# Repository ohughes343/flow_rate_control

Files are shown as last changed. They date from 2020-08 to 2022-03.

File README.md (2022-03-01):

# How To
You will need:
* Lulzbot TAZ 6 - This is the printer I based my design on, but the project could be modified for other printers
* Raspberry Pi - I wrote the code for a raspberry pi computer but with a few tweaks it can run on any computer. Just need a serial connection to the printer and a camera.
* Raspberry Pi HQ Camera
* 16mm lens - To zoom in on the filament
* Backlight - Important for accurate optical measurement. I strapped a flashlight on my printer but there is probably a more elegant solution.
* Red filament - I tuned the software to look for red pixels, but feel free to modify it for other colors

First, print my modified extruder latch and replace the original part with it.<br>

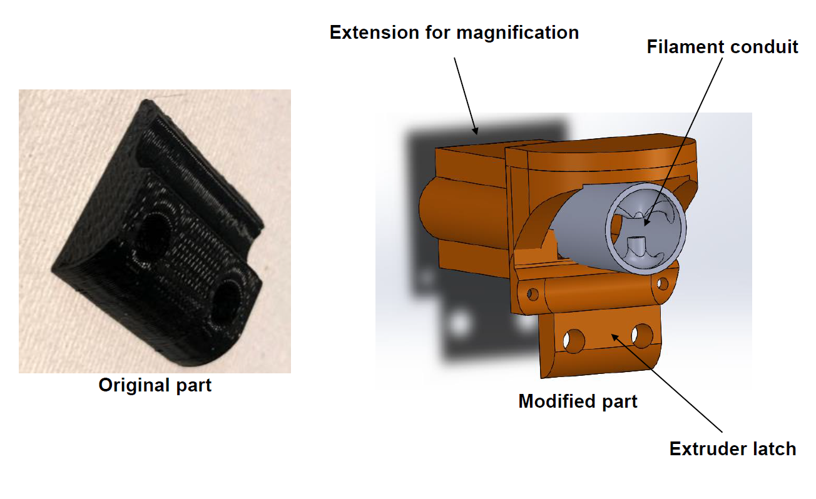
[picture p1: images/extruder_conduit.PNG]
Extruder Conduit


Next, print the extension for the camera lens. This is used to create a "macro" effect and zoom in on the filament. <br>
Be careful not to damage the camera sensor!<br>
Remove the camera lens and unscrew the black piece that holds the lens.<br>
Replace this with the printed extender, and then screw the lens back into that.<br>
You may want to test the camera to get a good zoom - the filament should fill up most of the frame.<br>

Next, download my modded version of pronterface onto your Raspberry Pi:<br>
```git clone https://github.com/ohughes343/flow_rate_control.git```

-Add your gcode file to the folder<br>
-Edit the measure.py file to include your gcode file: (filename="my_file.gcode")<br>
-Connect your Pi to the printer<br>
-Run the script! Print should start automatically<br>

# What is this?

The aim of this project was to produce high-quality prints *regardless of the quality of the filament.* 
Commercially available filament has tight tolerances (Prusa3D claims +/-0.02mm), but experimental filament is often much worse. Inconsistent diameter or consistently off diameter filament results in poor prints with inaccurate dimensions. To remedy this, I measured the filament diameter during printing and adjusted the flow rate accordingly.

This project should be able to print with filament that varies by as much as 0.2mm from its baseline. Outside those dimensions, the printer will have trouble grabbing the filament and may not extrude at all.

**How it works:** A camera attached to the printhead measures the diameter of the filament ten times per second. If the diameter varies too much, a command is sent to the printer to adjust its flow rate. The command is sent after a short delay as it takes some time for that section of filament to reach the nozzle. 
The code is run on a raspberry pi computer and uses pronterface http://www.pronterface.com/index.html

**Materials:**
* Lulzbot TAZ 6 - This is the printer I based my design on, but the project could be modified for other printers
* Raspberry Pi - I wrote the code for a raspberry pi computer but with a few tweaks it can run on any computer. Just need a serial connection to the printer and a camera.
* Raspberry Pi HQ Camera
* 16mm lens - To zoom in on the filament
* Backlight - Important for accurate optical measurement. I strapped a flashlight on my printer but there is probably a more elegant solution.

**Variable Diameter Filament**\
Print quality is related to fill factor, which requires careful control of extrusion rate. When printing, a normal printer assumes constant diameter filament. If diameter is inconsistent, extrudate diameter is also inconsistent.

![Deformed Filament](https://github.com/ohughes343/flow_rate_control/blob/master/images/deformed.JPG)

Tolerances are good for commercially produced filament, as low as ±0.02mm.
For experimental filament, however, the tolerances are typically more like ±0.2mm. This can result in low quality parts that are significantly weaker.

The goal of this project was to print high quality parts using lab-generated filament with ±0.2mm tolerances.

**Objective and Approach**\
Objective: Develop a low-cost, universal hardware and software modification that allows desktop printers to compensate for filament diameter variations

**Producing Variable Diameter Filament**\
I hung a 50cm length of filament and heated it with a hair dryer to produce necked down sections. I was careful to make sure the diameter stayed above 1.55mm, as the printer would not extrudate anything smaller. 

![Hairdryer](https://github.com/ohughes343/flow_rate_control/blob/master/images/hairdryer.png)

**Optical Imaging Setup**\
I purchased a Raspberry Pi 3 computer, an accompanying HQ camera, and a 16mm lens. I also downloaded an [extruder part](https://download.lulzbot.com/TAZ/6.02/production_parts/printed_parts/extruder_latch/) from Lulzbot and modified it to hold the camera and filament in place.

![Extruder Conduit](https://github.com/ohughes343/flow_rate_control/blob/master/images/extruder_conduit.PNG)

![Final setup on printhead](https://github.com/ohughes343/flow_rate_control/blob/master/images/final_setup.PNG)

**Optical Imaging Software**\
Images were captured and analyzed 10 times per second. Since the filament was moving at 1mm/s relative to the camera, 1mm of filament has 10 data points. I implemented a moving average to reduce noise - every data point is an average of itself and the previous 9 points.

![Before and after smoothing](https://github.com/ohughes343/flow_rate_control/blob/master/images/smoothing_graphs.png)

**Adaptive Algorithm**\
![Deformed Filament](https://github.com/ohughes343/flow_rate_control/blob/master/images/equations.png)

![Deformed Filament](https://github.com/ohughes343/flow_rate_control/blob/master/images/equation_graph.png)

**Pixel Size Calibration**\
I took images of filament and a microscope calibration slide at the same distance from the camera to calibrate my software. A 1.79mm diameter chunk of filament took up 508px, which is roughly 0.003mm/px. This is about the best resolution I could get while sampling 10x per second at 640x480. I was able to get 0.001mm/px resolution at lower sampling rates.

![Alt text](https://github.com/ohughes343/flow_rate_control/blob/master/images/filament_hd.JPG)

**Results: Optical Diameter Measurement**\
Measuring *the same* chunk of filament 3 times resulted in the plot on the left, demonstrating that my system is highly precise and repeatable. Some of the smoothing may be due to my software averaging, but it is clearly responding to real physical changes.
The plot on the right demonstrates the same idea with filament that was stretched out to produce very narrow sections.

In both cases, a digital micrometer confirmed the accuracy of the camera. 
![Variable Filament](https://github.com/ohughes343/flow_rate_control/blob/master/images/variable_diameter.png)

**Results: Adaptive Control**\
I implemented a delay in the system to account for the time it takes for the filament to travel from the camera to the nozzle. 
And this is where I got stuck. I first tried to use a time delay, but this wouldn't work for different speeds or if the motor ever retracted filament. A fixed step delay, which I tried next, is also complicated by retraction. So as of right now, the project *works*, but only if the motor never reverses.
![Variable Filament](https://github.com/ohughes343/flow_rate_control/blob/master/images/delay.png)

**My system vs a Keyence Laser**\
One chunk of **lab-produced** filament was measured 3 times with a Keyence digital micrometer. I measured the same chunk 3 times with my optical system to compare the results.
![Experimental](https://github.com/ohughes343/flow_rate_control/blob/master/images/experimental_vs_laser.png)

I made the same comparison with commercial filament.
![As-received](https://github.com/ohughes343/flow_rate_control/blob/master/images/as_received_vs_laser.png)

**Demonstration Part**\
I printed a thin airfoil part to demonstrate my adaptive control.
![Demo part](https://github.com/ohughes343/flow_rate_control/blob/master/images/demo_part.png) 

**Future Work**
* Universal Mount for other 3D printers
* Use with filament colors other than red

![FFF printer](https://github.com/ohughes343/flow_rate_control/blob/master/images/fff.png)

![Lulzbot TAZ 6](https://github.com/ohughes343/flow_rate_control/blob/master/images/taz.png)

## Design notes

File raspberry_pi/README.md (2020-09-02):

# flow_rate_control
If I published a paper it would be called something like *"Autonomous in-situ flow rate control of fused deposition modeling printers"*

Basically, the aim of this project is to produce high-quality prints regardless of the quality of the filament. 
Commercially available filament has tight tolerances (Prusa3D claims +/-0.02mm), but experimental filament is often much worse. Inconsistent diameter or consistently off diameter filament results in poor prints with inaccurate dimensions. There are even designs online to test for over/under extrusion: https://www.thingiverse.com/thing:1622868

This project should be able to print with filament that varies by as much as 0.2mm from its baseline. Outside those dimensions, the printer will have trouble grabbing the filament and may not extrude at all.

**How it works:** A camera attached to the printhead measures the diameter of the filament ten times per second. If the diameter varies too much, a command is sent to the printer to adjust its flow rate accordingly. The command is sent after a short delay, as it takes some time for that section of filament to reach the nozzle. 
The code is run on a raspberry pi computer and uses pronterface http://www.pronterface.com/index.html

**Materials:**
* Lulzbot TAZ 6 - This is just the printer I based my design on but the project could be modified for other printers
* Raspberry Pi - I wrote the code for a raspberry pi computer but with a few tweaks it can run on any computer. Just need a serial connection to the printer and a camera.
* Raspberry Pi HQ Camera
* 16mm lens - To zoom in on the filament
* Backlight - Important for accurate optical measurement. I strapped a flashlight on my printer but there is probably a more elegant solution.

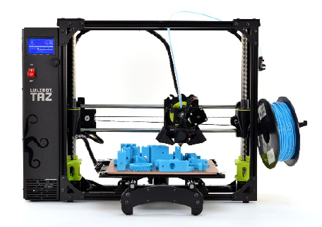
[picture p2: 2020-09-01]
images/taz.png

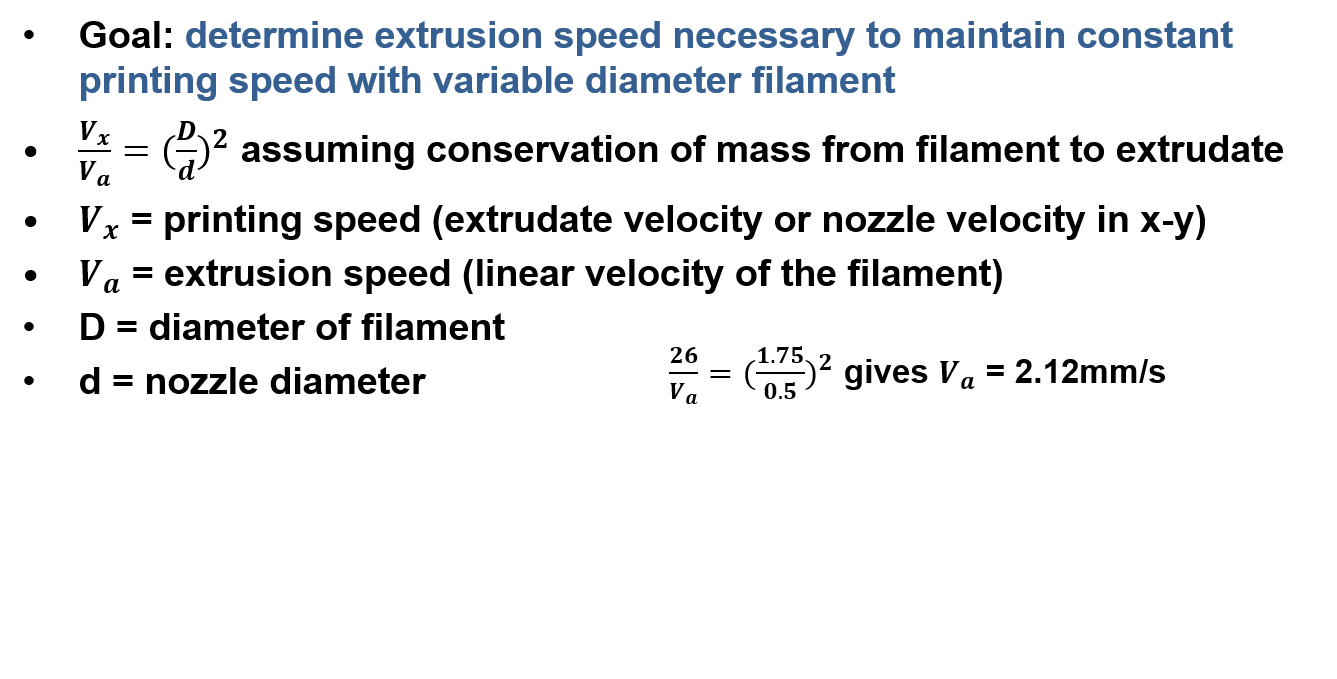
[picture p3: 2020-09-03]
images/equations.png

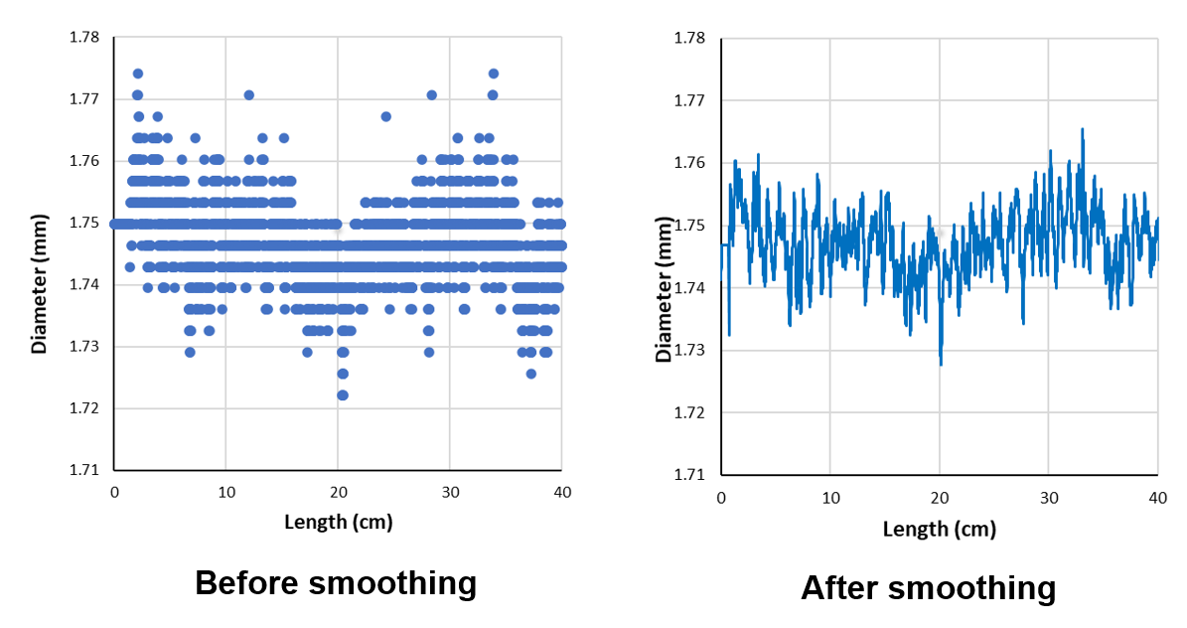
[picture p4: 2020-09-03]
images/smoothing_graphs.png

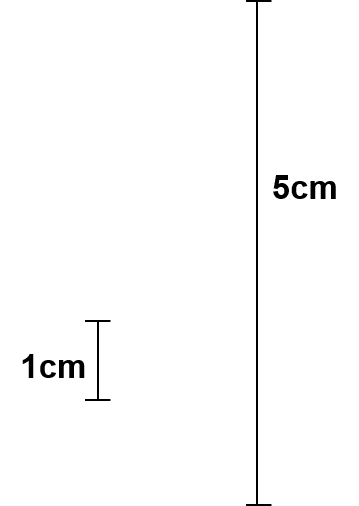
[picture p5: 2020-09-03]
images/filament_51.png

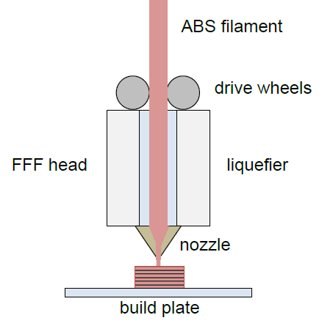
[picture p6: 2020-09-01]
images/fff.png

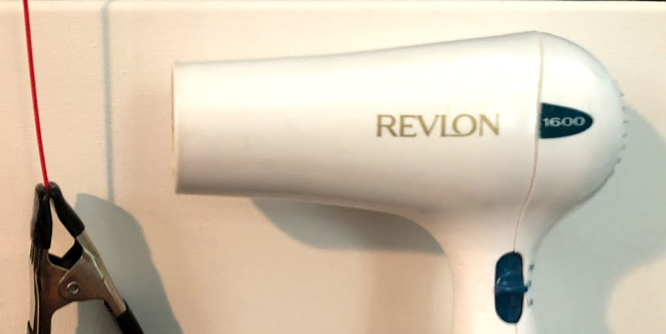
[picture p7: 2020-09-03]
images/hairdryer.png

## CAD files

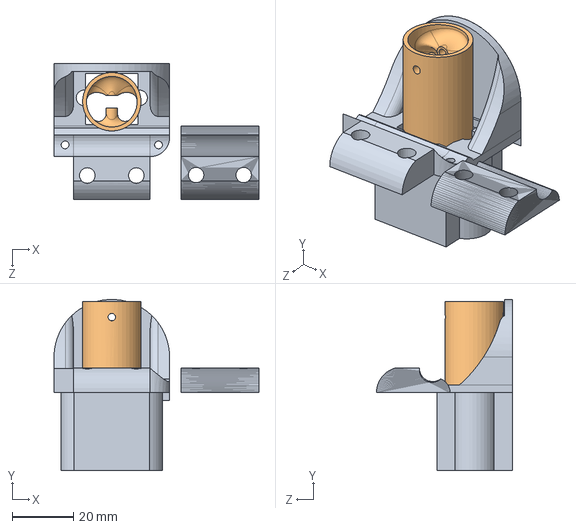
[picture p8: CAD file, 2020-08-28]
CAD files/camera_sleeve.SLDASM
66.8 x 55.8 x 44.4 mm
extruder_latch_largecamera
filament_lens_cap

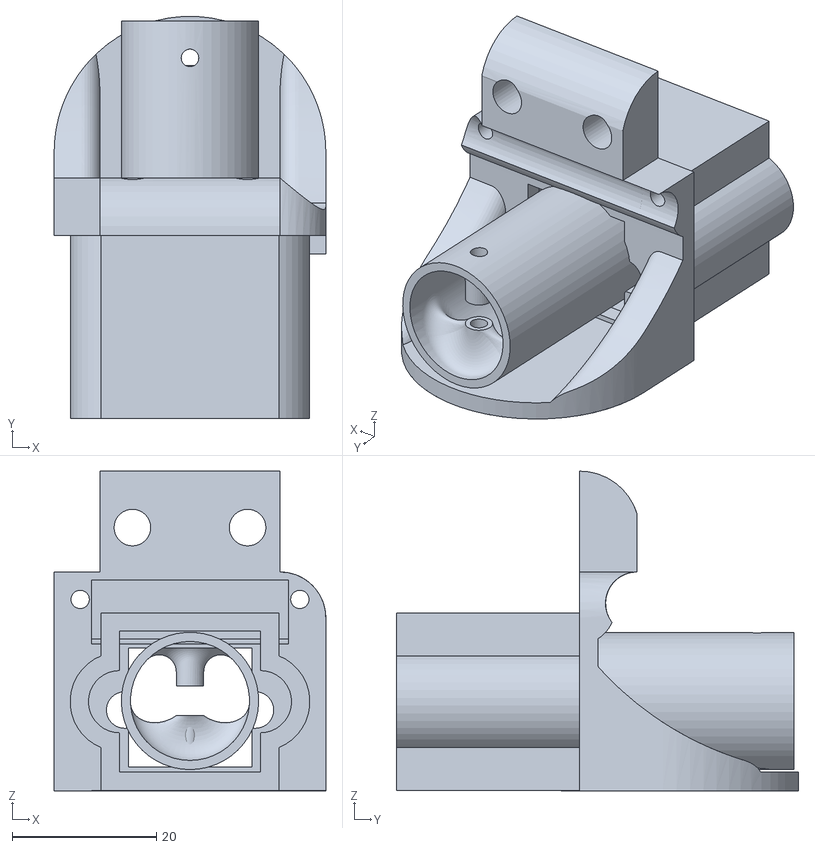
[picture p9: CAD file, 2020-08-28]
CAD files/camera_assembly_full.STL
37.7 x 55.8 x 44.4

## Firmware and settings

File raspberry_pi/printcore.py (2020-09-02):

#!/usr/bin/env python3

# This file is part of the Printrun suite.
#
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
import time
import getopt
import sys
import getopt

from printrun.printcore import printcore
from printrun.utils import setup_logging
from printrun import gcoder

if __name__ == '__main__':
    setup_logging(sys.stderr)
    baud = 250000
    loud = False
    statusreport = False

    from printrun.printcore import __version__ as printcore_version

    usage = "Usage:\n"+\
            "  printcore [OPTIONS] PORT FILE\n\n"+\
            "Options:\n"+\
            "  -b, --baud=BAUD_RATE"+\
                        "\t\tSet baud rate value. Default value is 115200\n"+\
            "  -s, --statusreport\t\tPrint progress as percentage\n"+\
            "  -v, --verbose\t\t\tPrint additional progress information\n"+\
            "  -V, --version\t\t\tPrint program's version number and exit\n"+\
            "  -h, --help\t\t\tPrint this help message and exit\n"

    try:
        opts, args = getopt.getopt(sys.argv[1:], "b:svVh",
                        ["baud=", "statusreport", "verbose", "version", "help"])
    except getopt.GetoptError as err:
        print(str(err))
        print(usage)
        sys.exit(2)
    for o, a in opts:
        if o in ('-h', '--help'):
            print(usage)
            sys.exit(0)
        elif o in ('-V','--version'):
            print("printrun "+printcore_version)
            sys.exit(0)
        elif o in ('-b','--baud'):
            try:
                baud = int(a)
            except ValueError:
                print("ValueError:")
                print("\tInvalid BAUD_RATE value '%s'" % a)
                print("\tBAUD_RATE must be an integer\n")
                # FIXME: This should output a more apropiate error message when
                #        not a good baud rate is passed as an argument
                #        i.e: when baud <= 1000 or > 225000
                print(usage)
                sys.exit(2)
        elif o in ('-v', '--verbose'):
            loud = True
        elif o in ('-s', '--statusreport'):
            statusreport = True

    if len(args) <= 1:
        print("Error: Port or gcode file were not specified.\n")
        print(usage)
        sys.exit(2)
    elif len(args) > 1:
        port = args[-2]
        filename = args[-1]
        print("Printing: %s on %s with baudrate %d" % (filename, port, baud))

    p = printcore(port, baud)
    p.loud = loud
    time.sleep(2)
    gcode = [i.strip() for i in open(filename)]
    gcode = gcoder.LightGCode(gcode)
    p.startprint(gcode)

    try:
        if statusreport:
            p.loud = False
            sys.stdout.write("Progress: 00.0%\r")
            sys.stdout.flush()
        while p.printing:
            time.sleep(1)
            if statusreport:
                progress = 100 * float(p.queueindex) / len(p.mainqueue)
                sys.stdout.write("Progress: %02.1f%%\r" % progress)
                sys.stdout.flush()
        p.disconnect()
        sys.exit(0)
    except:
        p.disconnect()

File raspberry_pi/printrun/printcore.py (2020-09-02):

# This file is part of the Printrun suite.
#
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
__version__ = "2.0.0rc6"

import sys
if sys.version_info.major < 3:
    print("You need to run this on Python 3")
    sys.exit(-1)

from serial import Serial, SerialException, PARITY_ODD, PARITY_NONE
from select import error as SelectError
import threading
from queue import Queue, Empty as QueueEmpty
import time
import platform
import os
import logging
import traceback
import errno
import socket
import re
import selectors
from functools import wraps, reduce
from collections import deque
from printrun import gcoder
from .utils import set_utf8_locale, install_locale, decode_utf8
try:
    set_utf8_locale()
except:
    pass
install_locale('pronterface')
from printrun.plugins import PRINTCORE_HANDLER

def locked(f):
    @wraps(f)
    def inner(*args, **kw):
        with inner.lock:
            return f(*args, **kw)
    inner.lock = threading.Lock()
    return inner

def control_ttyhup(port, disable_hup):
    """Controls the HUPCL"""
    if platform.system() == "Linux":
        if disable_hup:
            os.system("stty -F %s -hup" % port)
        else:
            os.system("stty -F %s hup" % port)

def enable_hup(port):
    control_ttyhup(port, False)

def disable_hup(port):
    control_ttyhup(port, True)

PR_EOF = None  #printrun's marker for EOF
PR_AGAIN = b'' #printrun's marker for timeout/no data
SYS_EOF = b''  #python's marker for EOF
SYS_AGAIN = None #python's marker for timeout/no data

class printcore():
    def __init__(self, port = None, baud = None, dtr=None):
        """Initializes a printcore instance. Pass the port and baud rate to
           connect immediately"""
        self.baud = None
        self.dtr = None
        self.port = None
        self.analyzer = gcoder.GCode()
        # Serial instance connected to the printer, should be None when
        # disconnected
        self.printer = None
        # clear to send, enabled after responses
        # FIXME: should probably be changed to a sliding window approach
        self.clear = 0
        # The printer has responded to the initial command and is active
        self.online = False
        # is a print currently running, true if printing, false if paused
        self.printing = False
        self.mainqueue = None
        self.priqueue = Queue(0)
        self.queueindex = 0
        self.lineno = 0
        self.resendfrom = -1
        self.paused = False
        self.sentlines = {}
        self.log = deque(maxlen = 10000)
        self.sent = []
        self.writefailures = 0
        self.tempcb = None  # impl (wholeline)
        self.recvcb = None  # impl (wholeline)
        self.sendcb = None  # impl (wholeline)
        self.preprintsendcb = None  # impl (wholeline)
        self.printsendcb = None  # impl (wholeline)
        self.layerchangecb = None  # impl (wholeline)
        self.errorcb = None  # impl (wholeline)
        self.startcb = None  # impl ()
        self.endcb = None  # impl ()
        self.onlinecb = None  # impl ()
        self.loud = False  # emit sent and received lines to terminal
        self.tcp_streaming_mode = False
        self.greetings = ['start', 'Grbl ']
        self.wait = 0  # default wait period for send(), send_now()
        self.read_thread = None
        self.stop_read_thread = False
        self.send_thread = None
        self.stop_send_thread = False
        self.print_thread = None
        self.readline_buf = []
        self.selector = None
        self.event_handler = PRINTCORE_HANDLER
        # Not all platforms need to do this parity workaround, and some drivers
        # don't support it.  Limit it to platforms that actually require it
        # here to avoid doing redundant work elsewhere and potentially breaking
        # things.
        self.needs_parity_workaround = platform.system() == "linux" and os.path.exists("/etc/debian")
        for handler in self.event_handler:
            try: handler.on_init()
            except: logging.error(traceback.format_exc())
        if port is not None and baud is not None:
            self.connect(port, baud)
        self.xy_feedrate = None
        self.z_feedrate = None

    def addEventHandler(self, handler):
        '''
        Adds an event handler.
        
        @param handler: The handler to be added.
        '''
        self.event_handler.append(handler)

    def logError(self, error):
        for handler in self.event_handler:
            try: handler.on_error(error)
            except: logging.error(traceback.format_exc())
        if self.errorcb:
            try: self.errorcb(error)
            except: logging.error(traceback.format_exc())
        else:
            logging.error(error)

    @locked
    def disconnect(self):
        """Disconnects from printer and pauses the print
        """
        if self.printer:
            if self.read_thread:
                self.stop_read_thread = True
                if threading.current_thread() != self.read_thread:
                    self.read_thread.join()
                self.read_thread = None
            if self.print_thread:
                self.printing = False
                self.print_thread.join()
            self._stop_sender()
            try:
                if self.selector is not None:
                    self.selector.unregister(self.printer_tcp)
                    self.selector.close()
                    self.selector = None
                if self.printer_tcp is not None:
                    self.printer_tcp.close()
                    self.printer_tcp = None
                self.printer.close()
            except socket.error:
                logger.error(traceback.format_exc())
                pass
            except OSError:
                logger.error(traceback.format_exc())
                pass
        for handler in self.event_handler:
            try: handler.on_disconnect()
            except: logging.error(traceback.format_exc())
        self.printer = None
        self.online = False
        self.printing = False
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

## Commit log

2020-09-02 readding raspberry_pi/
2020-09-07 created DATA folder and added laser-optical comparison
    [compare_laser_optical.xls]
2020-10-29 laser comparison images
2020-10-29 images of the extruder conduit

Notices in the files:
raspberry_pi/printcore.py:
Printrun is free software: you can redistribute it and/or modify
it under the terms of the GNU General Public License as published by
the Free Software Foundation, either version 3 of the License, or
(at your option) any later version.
